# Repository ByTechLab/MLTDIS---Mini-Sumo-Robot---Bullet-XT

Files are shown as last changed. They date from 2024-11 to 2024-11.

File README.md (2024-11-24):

<div align="center">
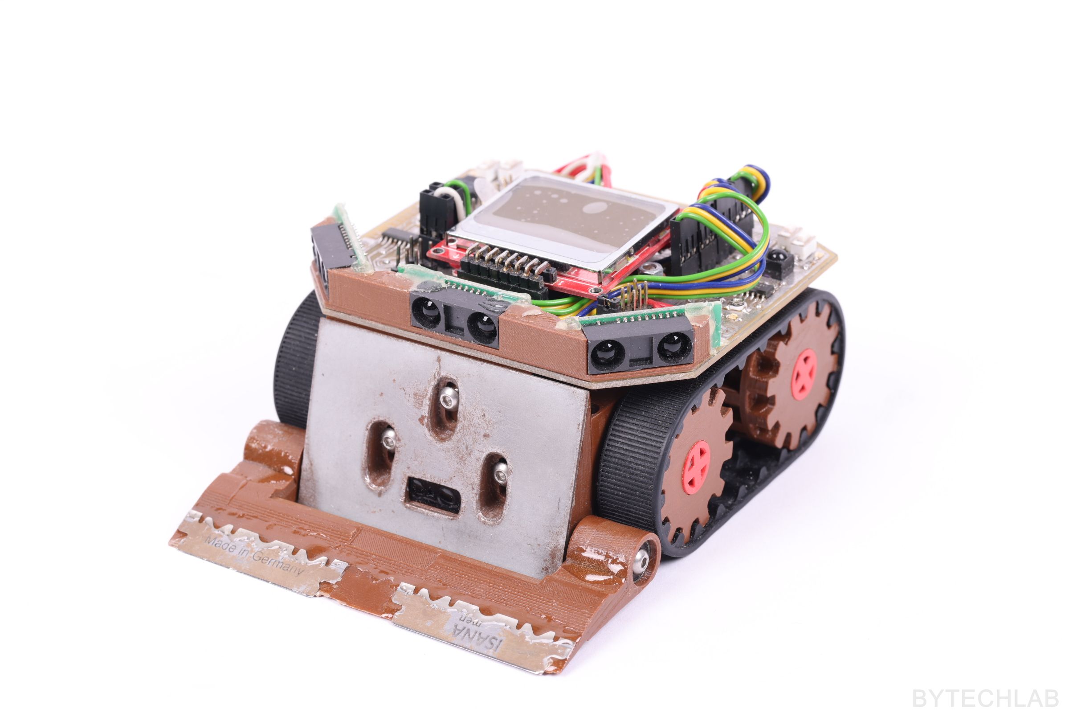
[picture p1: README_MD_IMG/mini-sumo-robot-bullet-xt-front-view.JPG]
project photo
    
</div>

Mini sumo robot - Bullet XT.

### Read more at BYTECHLAB:

<table style="width: 100%; border: none;" cellspacing="0" cellpadding="0" border="0">
  <tr>
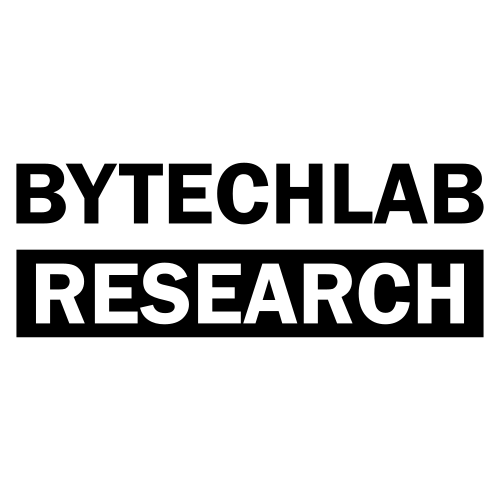
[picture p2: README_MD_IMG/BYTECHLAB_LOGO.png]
    <td></td>
    <td>https://bytechlab.com/2017/09/minisumo-bullet-xt/</td>
  </tr>
</table>

## License
Software \ Firmware:



Hardware \ Hardware design files \ Hardware documentation:

[][cc-by-nc-sa]

[Creative Commons Attribution-NonCommercial-ShareAlike 4.0 International License][cc-by-nc-sa].

[][cc-by-nc-sa]

[cc-by-nc-sa]: http://creativecommons.org/licenses/by-nc-sa/4.0/
[cc-by-nc-sa-image]: https://licensebuttons.net/l/by-nc-sa/4.0/88x31.png
[cc-by-nc-sa-shield]: https://img.shields.io/badge/License-CC%20BY--NC--SA%204.0-lightgrey.svg

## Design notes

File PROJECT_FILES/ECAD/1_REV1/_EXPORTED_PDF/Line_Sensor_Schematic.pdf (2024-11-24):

## 24.11.2024 15:51 (Sheet: 1/1)

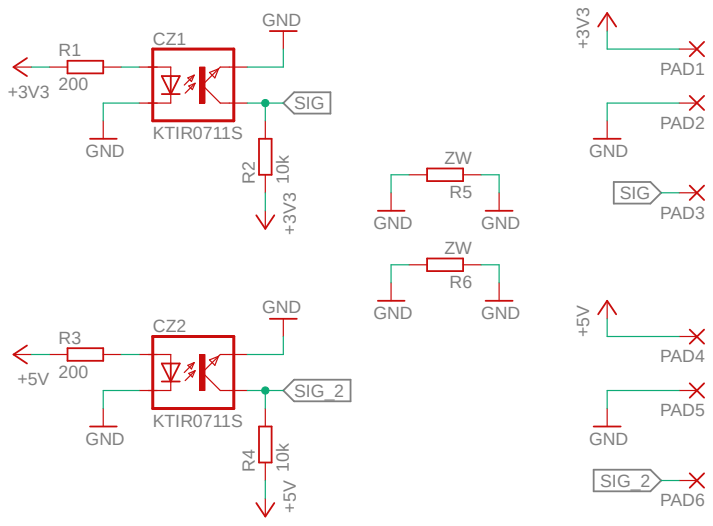
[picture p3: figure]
KTIR0711S; GND; PAD1; PAD2; PAD3; PAD4; PAD5; PAD6; SIG; SIG_2

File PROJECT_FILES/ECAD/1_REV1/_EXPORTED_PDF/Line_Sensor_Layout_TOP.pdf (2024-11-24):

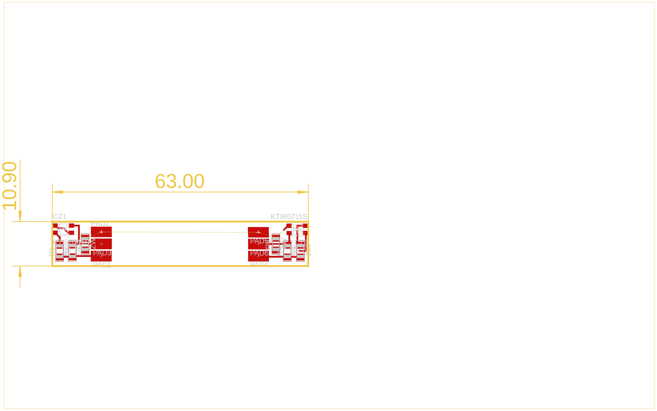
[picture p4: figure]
PAD1; PAD2 R¹; PAD4; KTIR0711S; KTIR0711S 200 10.90

24.11.2024 15:52

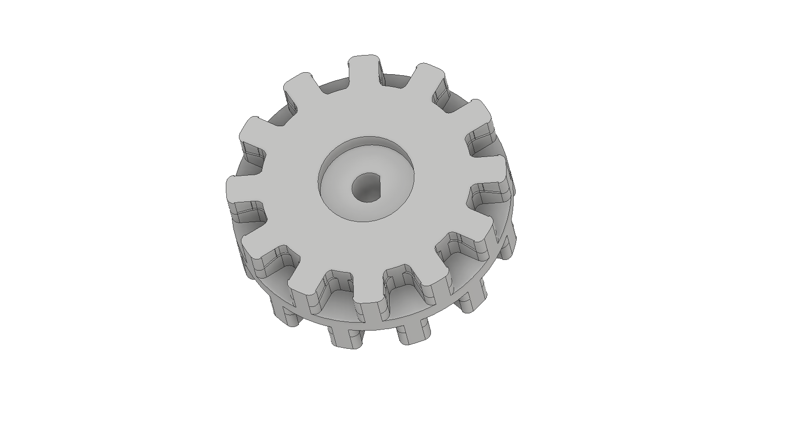
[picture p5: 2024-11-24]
PROJECT_FILES/MCAD/1_REV1/_RENDERS_EXPORTED/3DP_PLA_Motor_wheel.bmp

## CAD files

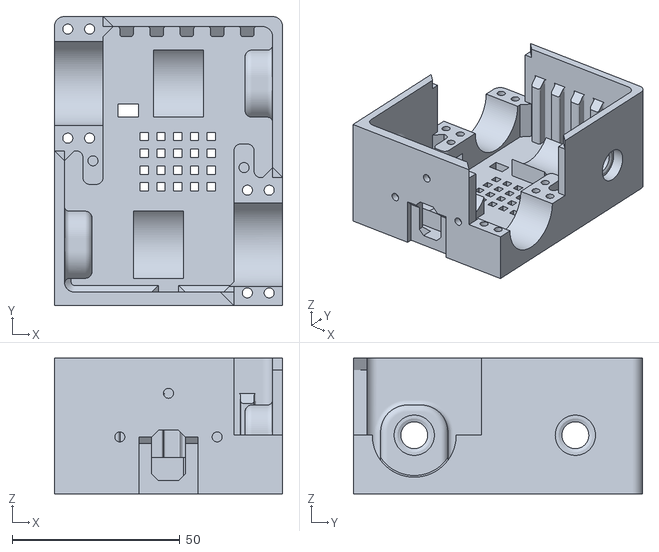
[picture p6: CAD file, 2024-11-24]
PROJECT_FILES/MCAD/1_REV1/_STL_EXPORTED/3DP_PLA_Main_frame.stl
68.0 x 86.1 x 40.5

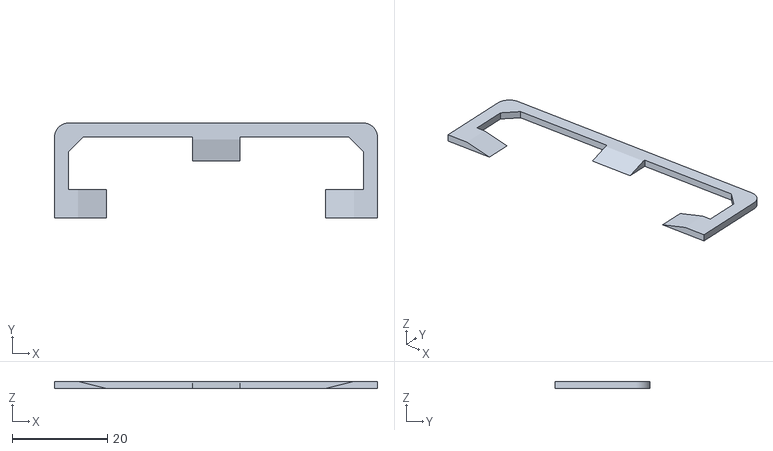
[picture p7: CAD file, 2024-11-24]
PROJECT_FILES/MCAD/1_REV1/_STL_EXPORTED/3DP_PLA_Back_slider.stl
68.0 x 20.0 x 1.50

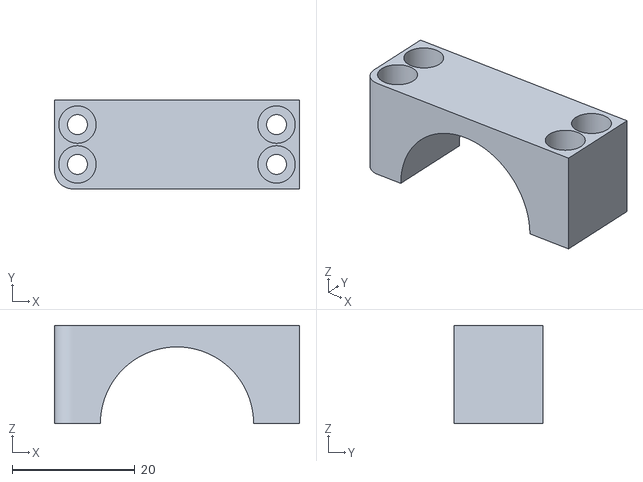
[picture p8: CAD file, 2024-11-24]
PROJECT_FILES/MCAD/1_REV1/_STL_EXPORTED/3DP_PLA_Motor_mounting_bracket_back.stl
40.0 x 14.5 x 16.0

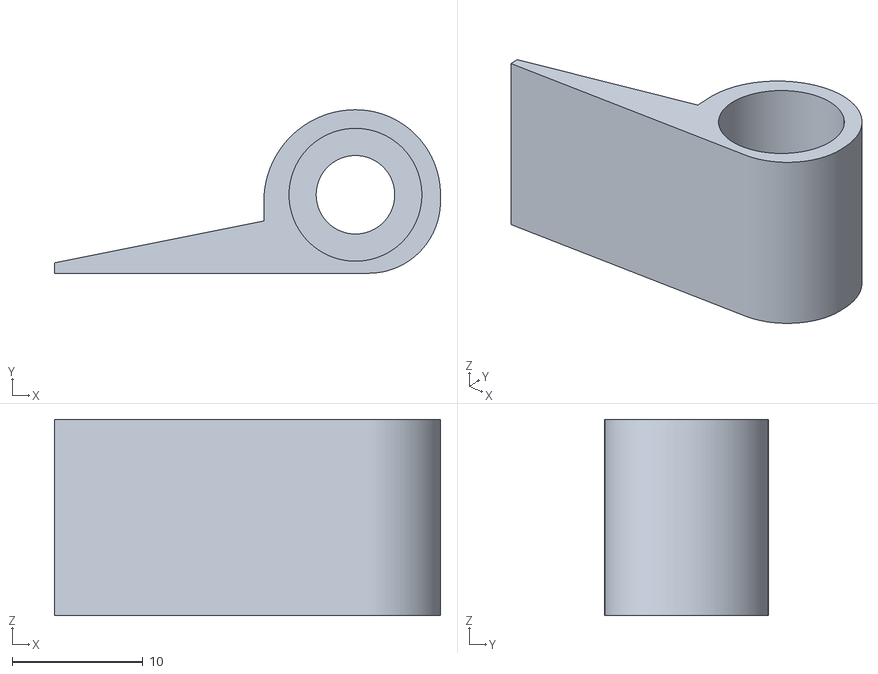
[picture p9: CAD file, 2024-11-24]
PROJECT_FILES/MCAD/1_REV1/_STL_EXPORTED/3DP_PLA_Front_blade_hinge_mir.stl
29.5 x 12.5 x 15.0

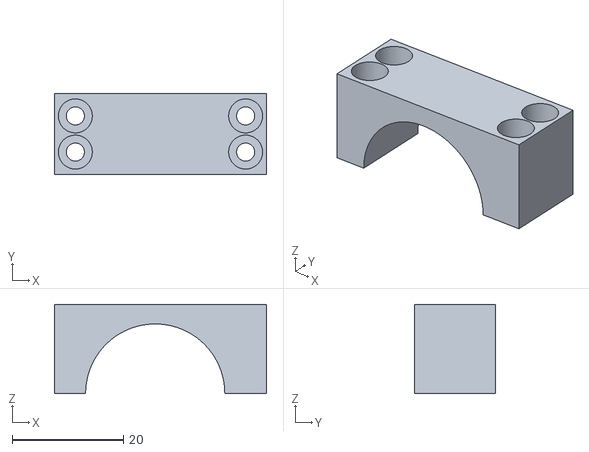
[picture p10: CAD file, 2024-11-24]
PROJECT_FILES/MCAD/1_REV1/_STL_EXPORTED/3DP_PLA_Motor_mounting_bracket_front.stl
38.1 x 14.5 x 16.0

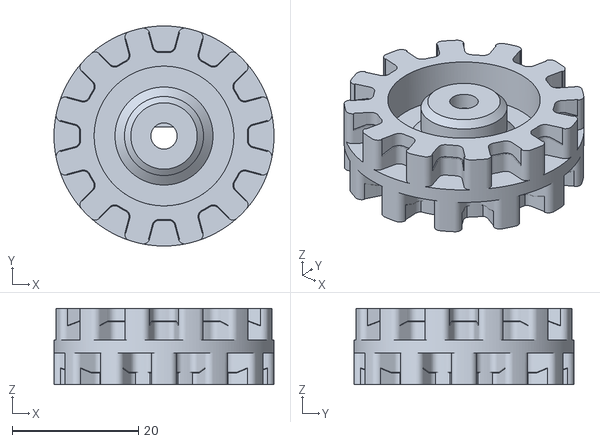
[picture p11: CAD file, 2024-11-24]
PROJECT_FILES/MCAD/1_REV1/_STL_EXPORTED/3DP_PLA_Motor_wheel.stl
34.8 x 34.8 x 12.0

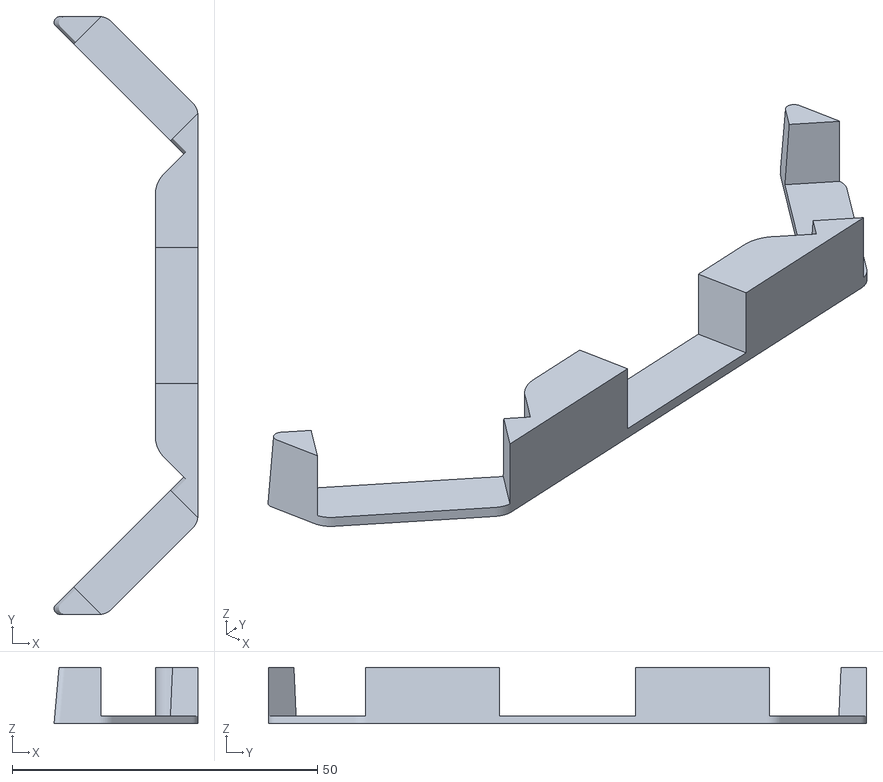
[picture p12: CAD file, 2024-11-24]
PROJECT_FILES/MCAD/1_REV1/_STL_EXPORTED/3DP_PLA_Front_Sharp_sensors_mounting_bracket.stl
23.6 x 98.0 x 9.20

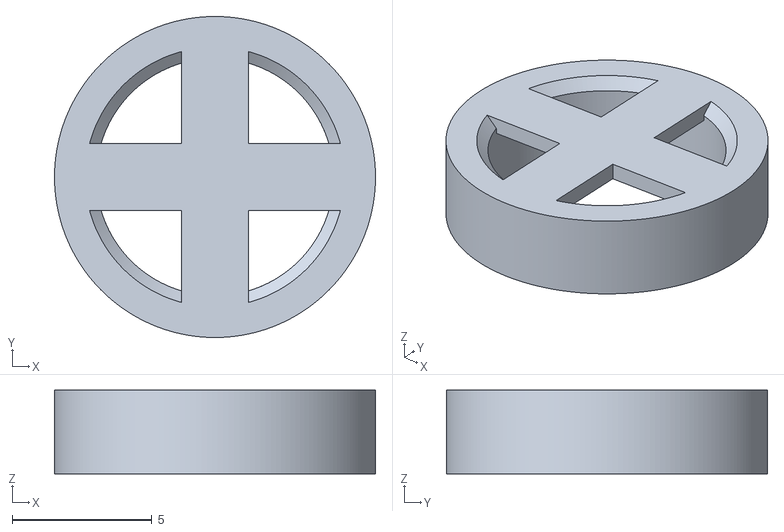
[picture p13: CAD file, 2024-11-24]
PROJECT_FILES/MCAD/1_REV1/_STL_EXPORTED/3DP_PLA_Wheel_cover.stl
11.5 x 11.5 x 3.00

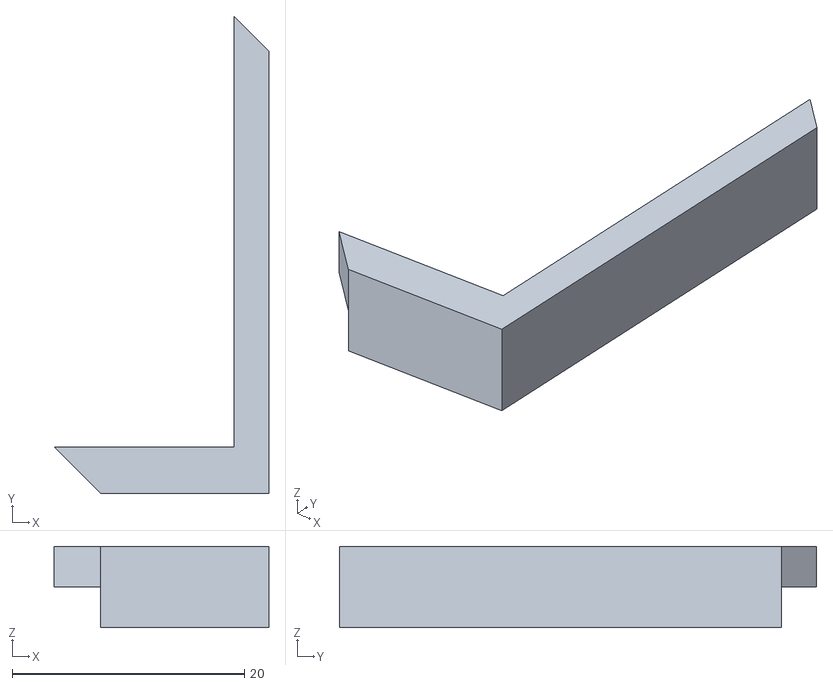
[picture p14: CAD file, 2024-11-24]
PROJECT_FILES/MCAD/1_REV1/_STL_EXPORTED/3DP_PLA_Front_motor_clamp_hole_plug.stl
18.5 x 41.1 x 7.00

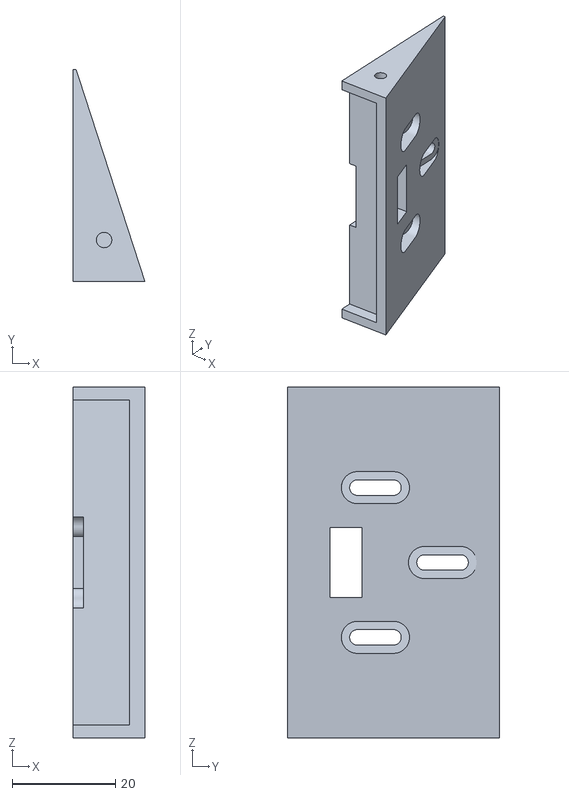
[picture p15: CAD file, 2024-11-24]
PROJECT_FILES/MCAD/1_REV1/_STL_EXPORTED/3DP_PLA_Front_plow.stl
13.9 x 41.0 x 68.0

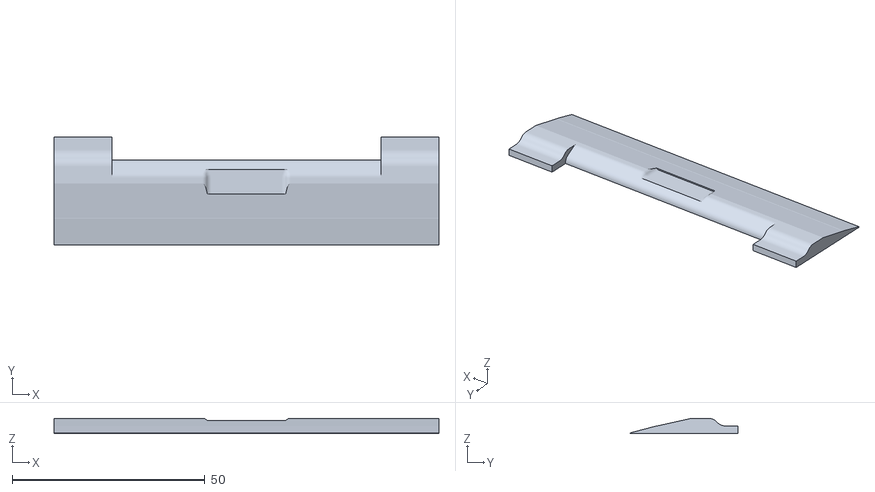
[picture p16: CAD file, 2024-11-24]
PROJECT_FILES/MCAD/1_REV1/_STL_EXPORTED/3DP_PLA_Front_blade.stl
100.0 x 28.0 x 4.00

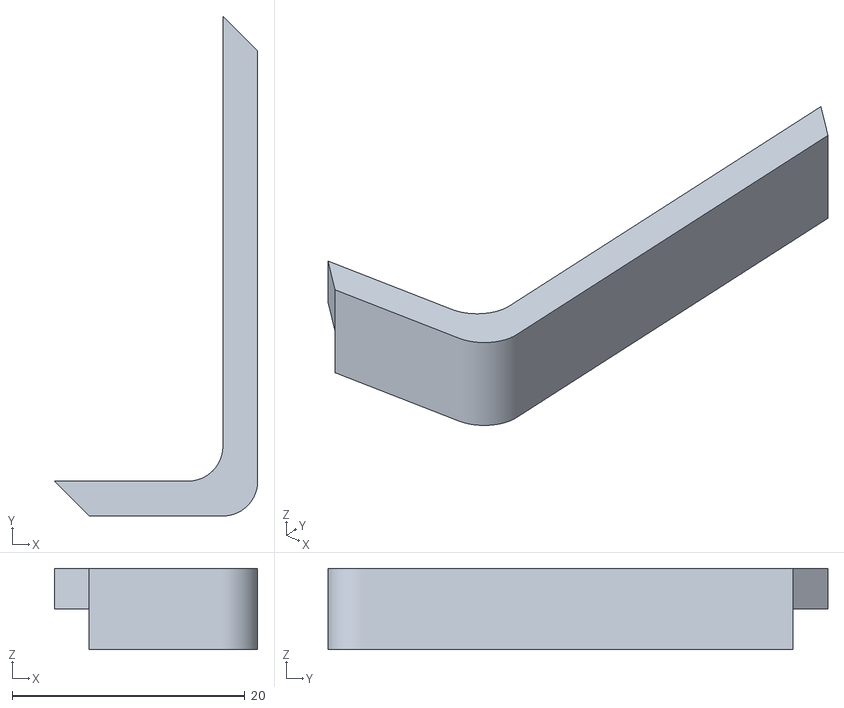
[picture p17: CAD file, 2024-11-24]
PROJECT_FILES/MCAD/1_REV1/_STL_EXPORTED/3DP_PLA_Back_motor_clamp_hole_plug.stl
17.5 x 43.0 x 7.00

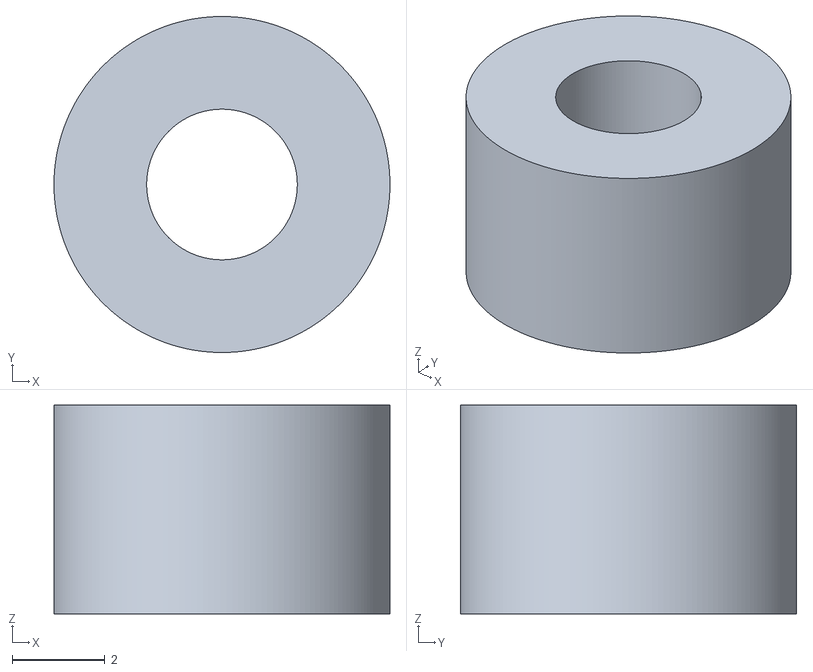
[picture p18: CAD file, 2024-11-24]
PROJECT_FILES/MCAD/1_REV1/_STL_EXPORTED/3DP_PLA_M3_screw_washer.stl
7.25 x 7.25 x 4.50

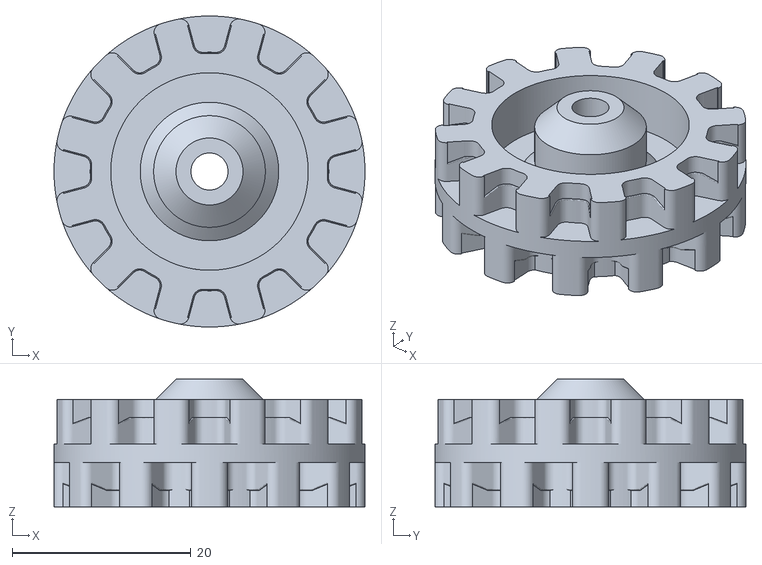
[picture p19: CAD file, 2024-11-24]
PROJECT_FILES/MCAD/1_REV1/_STL_EXPORTED/3DP_PLA_Screw_wheel.stl
34.8 x 34.8 x 14.3

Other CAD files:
PROJECT_FILES/MCAD/1_REV1/_STL_EXPORTED/3DP_PLA_Front_blade_hinge.stl
PROJECT_FILES/MCAD/1_REV1/ASSEMBLY_MAIN_REVA/3DP_PLA_Back_motor_clamp_hole_plug.ipt
PROJECT_FILES/MCAD/1_REV1/ASSEMBLY_MAIN_REVA/3DP_PLA_Back_slider.ipt
PROJECT_FILES/MCAD/1_REV1/ASSEMBLY_MAIN_REVA/3DP_PLA_Front_Sharp_sensors_mounting_bracket.ipt
PROJECT_FILES/MCAD/1_REV1/ASSEMBLY_MAIN_REVA/3DP_PLA_Front_blade.ipt
PROJECT_FILES/MCAD/1_REV1/ASSEMBLY_MAIN_REVA/3DP_PLA_Front_blade_hinge.ipt
PROJECT_FILES/MCAD/1_REV1/ASSEMBLY_MAIN_REVA/3DP_PLA_Front_blade_hinge_mir.ipt
PROJECT_FILES/MCAD/1_REV1/ASSEMBLY_MAIN_REVA/3DP_PLA_Front_motor_clamp_hole_plug.ipt
PROJECT_FILES/MCAD/1_REV1/ASSEMBLY_MAIN_REVA/3DP_PLA_Front_plow.ipt
PROJECT_FILES/MCAD/1_REV1/ASSEMBLY_MAIN_REVA/3DP_PLA_M3_screw_washer.ipt
PROJECT_FILES/MCAD/1_REV1/ASSEMBLY_MAIN_REVA/3DP_PLA_Main_frame.ipt
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

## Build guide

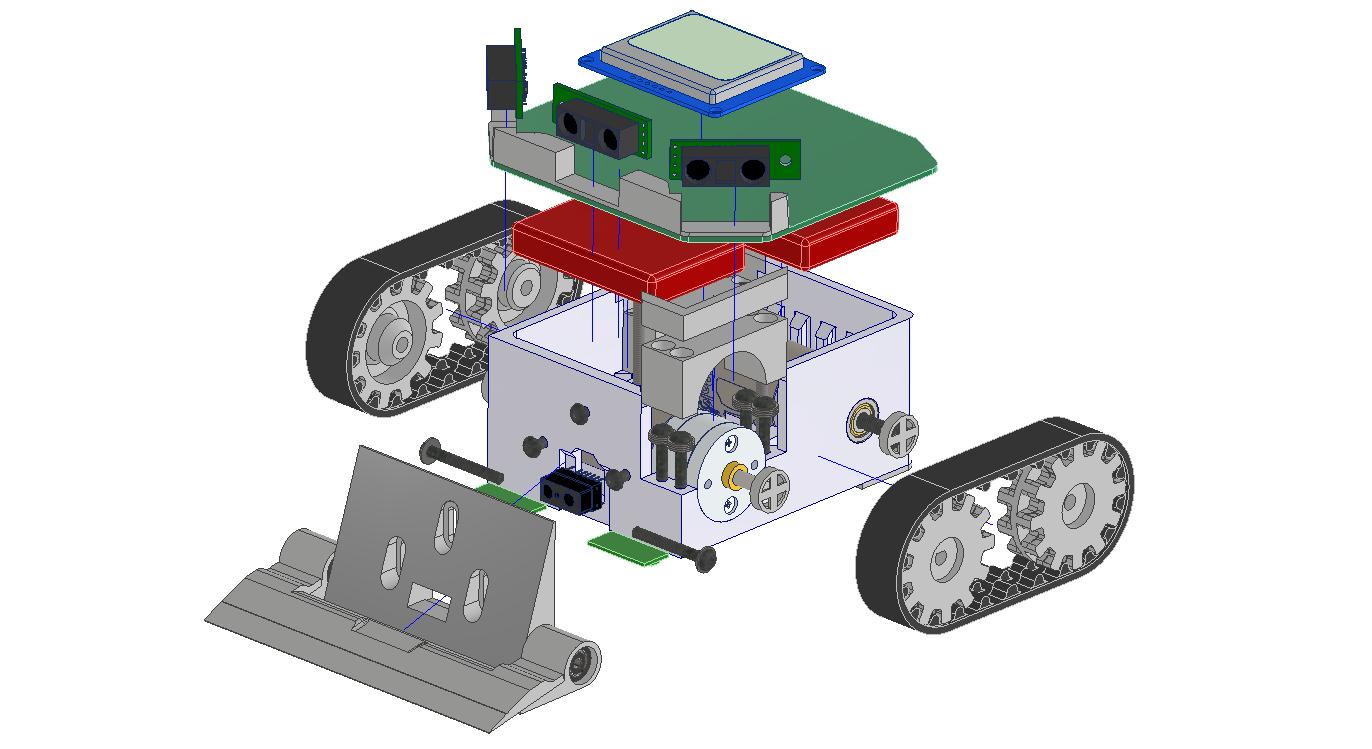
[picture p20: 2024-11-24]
PROJECT_FILES/MCAD/1_REV1/_RENDERS_EXPORTED/ASSEMBLY_Main_4.bmp

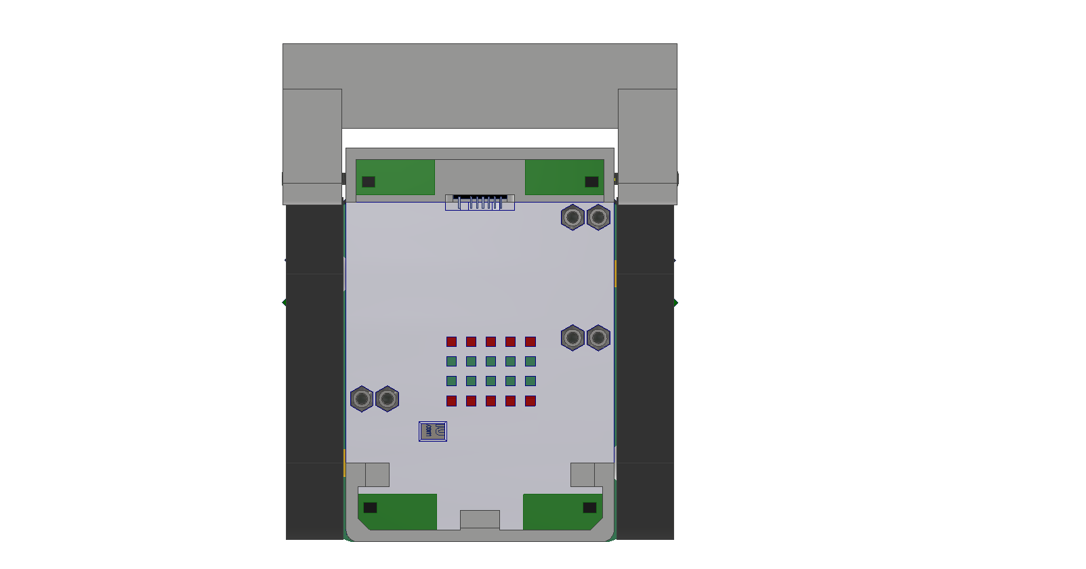
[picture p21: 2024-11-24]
PROJECT_FILES/MCAD/1_REV1/_RENDERS_EXPORTED/ASSEMBLY_Main_3.bmp

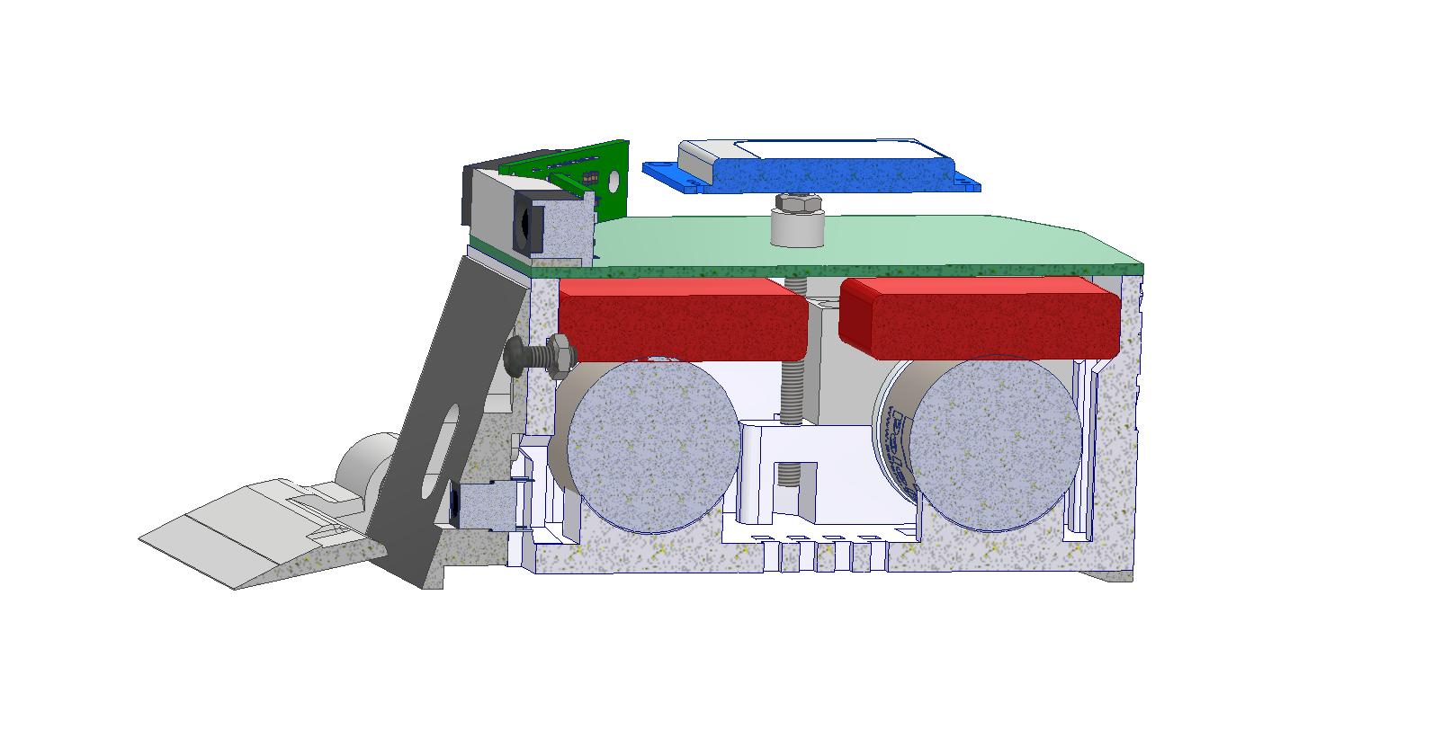
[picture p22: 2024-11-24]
PROJECT_FILES/MCAD/1_REV1/_RENDERS_EXPORTED/ASSEMBLY_Main_2.bmp

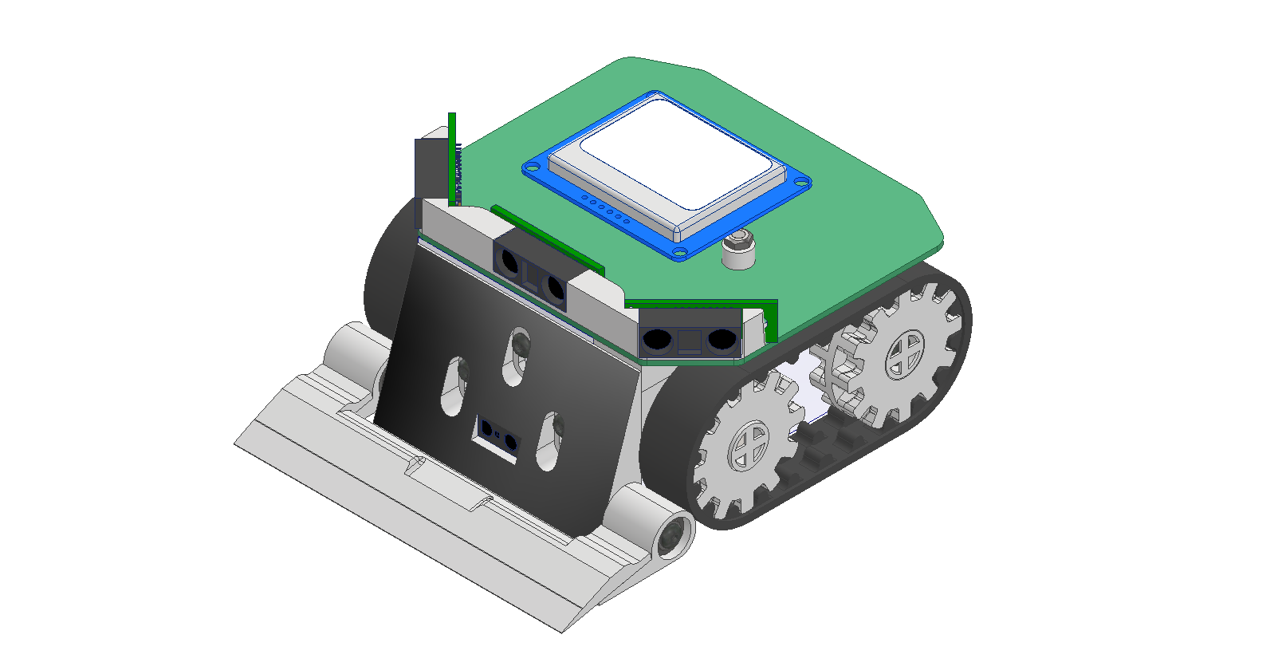
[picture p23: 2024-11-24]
PROJECT_FILES/MCAD/1_REV1/_RENDERS_EXPORTED/ASSEMBLY_Main.bmp

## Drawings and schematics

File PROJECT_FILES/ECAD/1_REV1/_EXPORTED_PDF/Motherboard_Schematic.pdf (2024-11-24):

# GND BATV BATV

## BUZZER

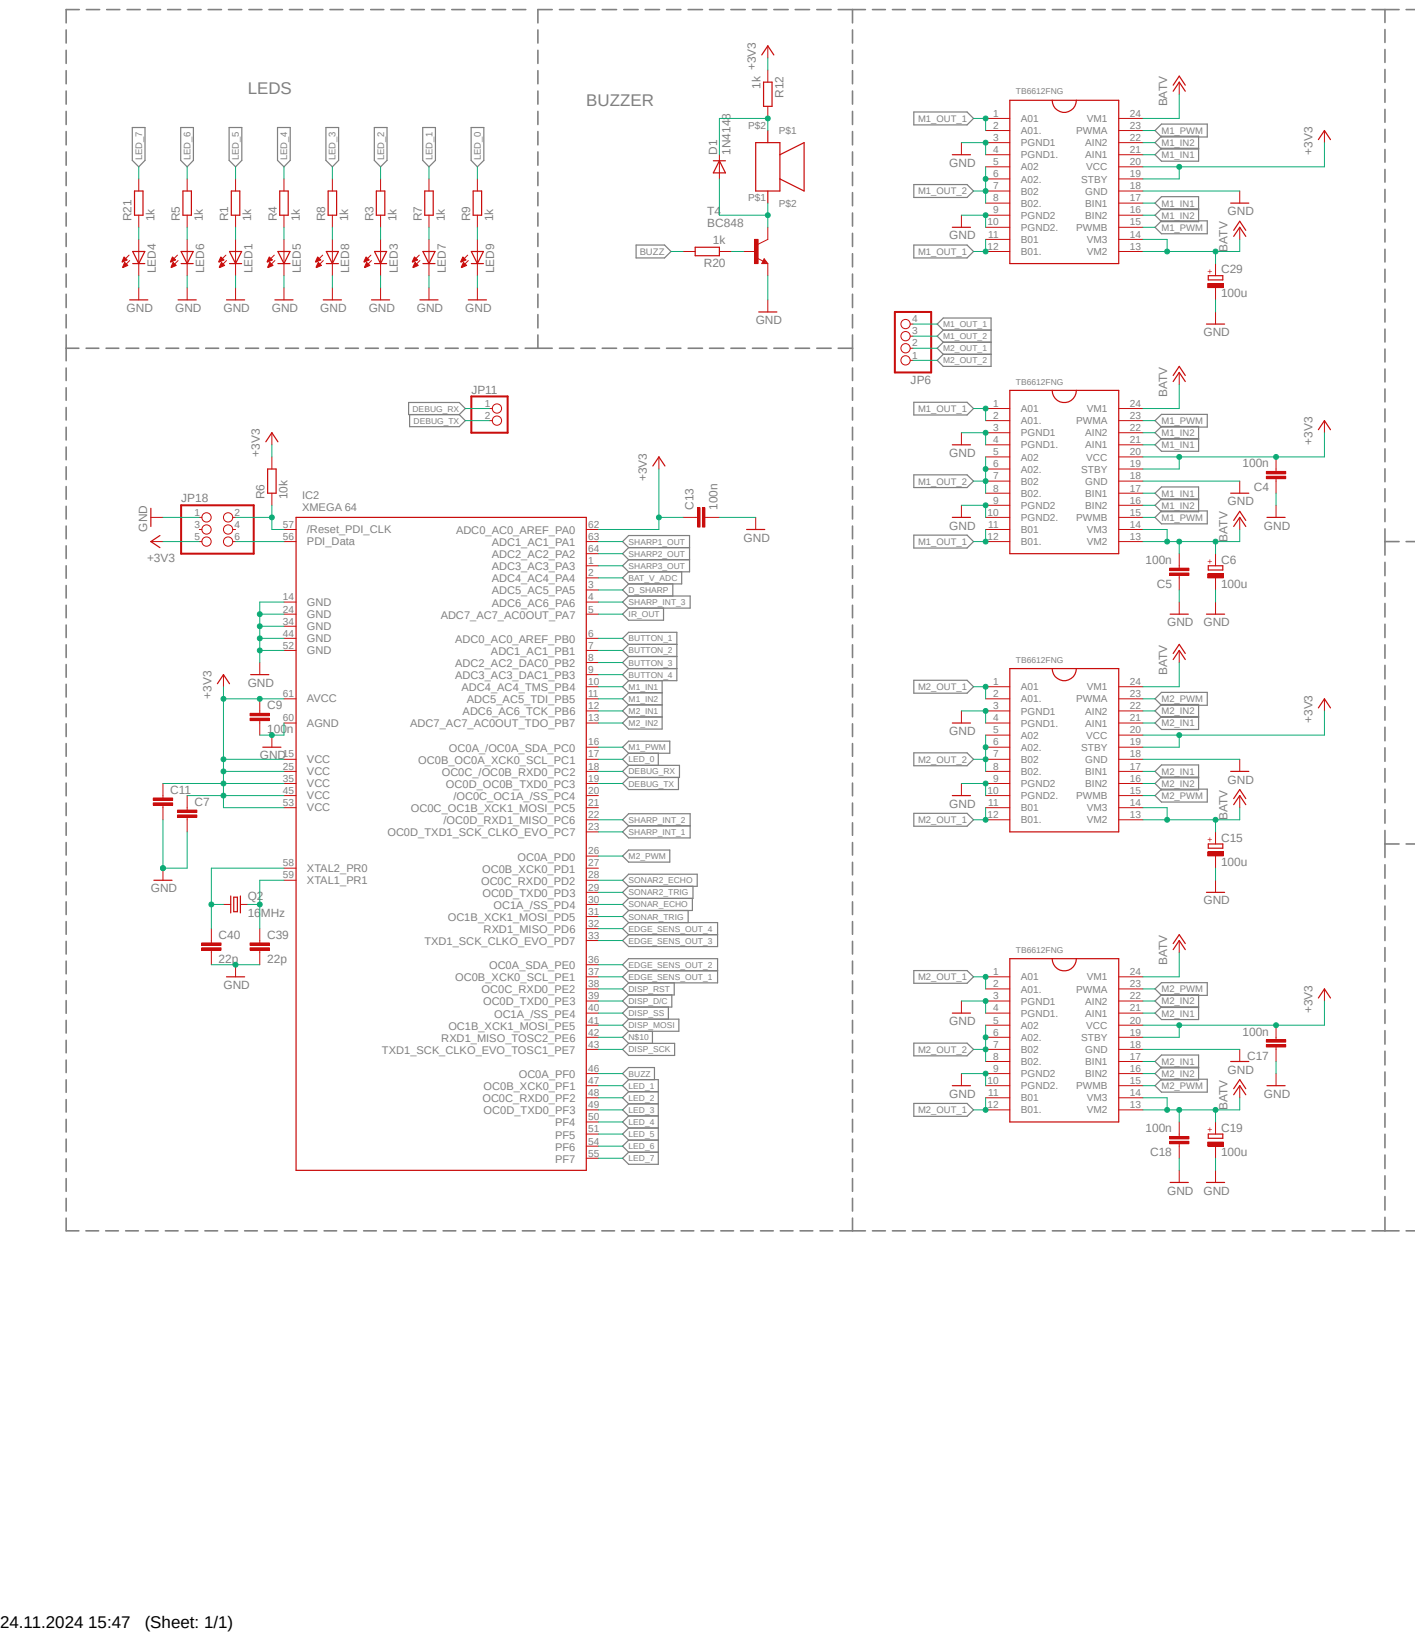
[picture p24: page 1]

45
53

## EDGE SENS

IR

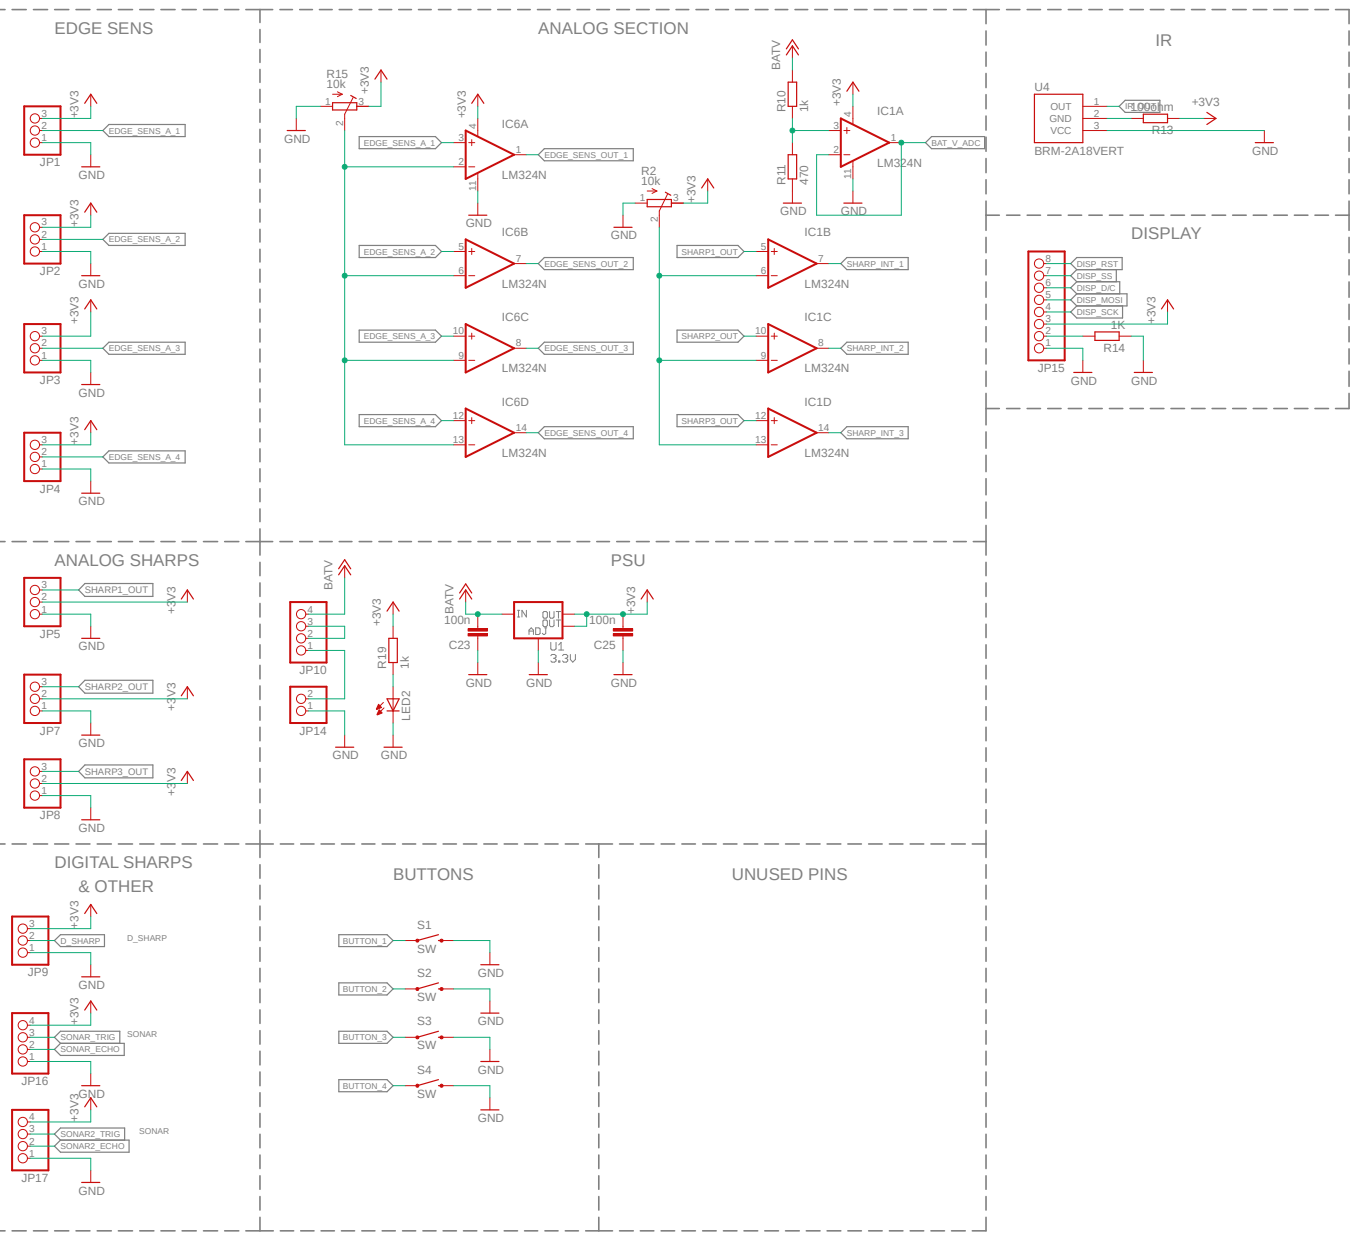
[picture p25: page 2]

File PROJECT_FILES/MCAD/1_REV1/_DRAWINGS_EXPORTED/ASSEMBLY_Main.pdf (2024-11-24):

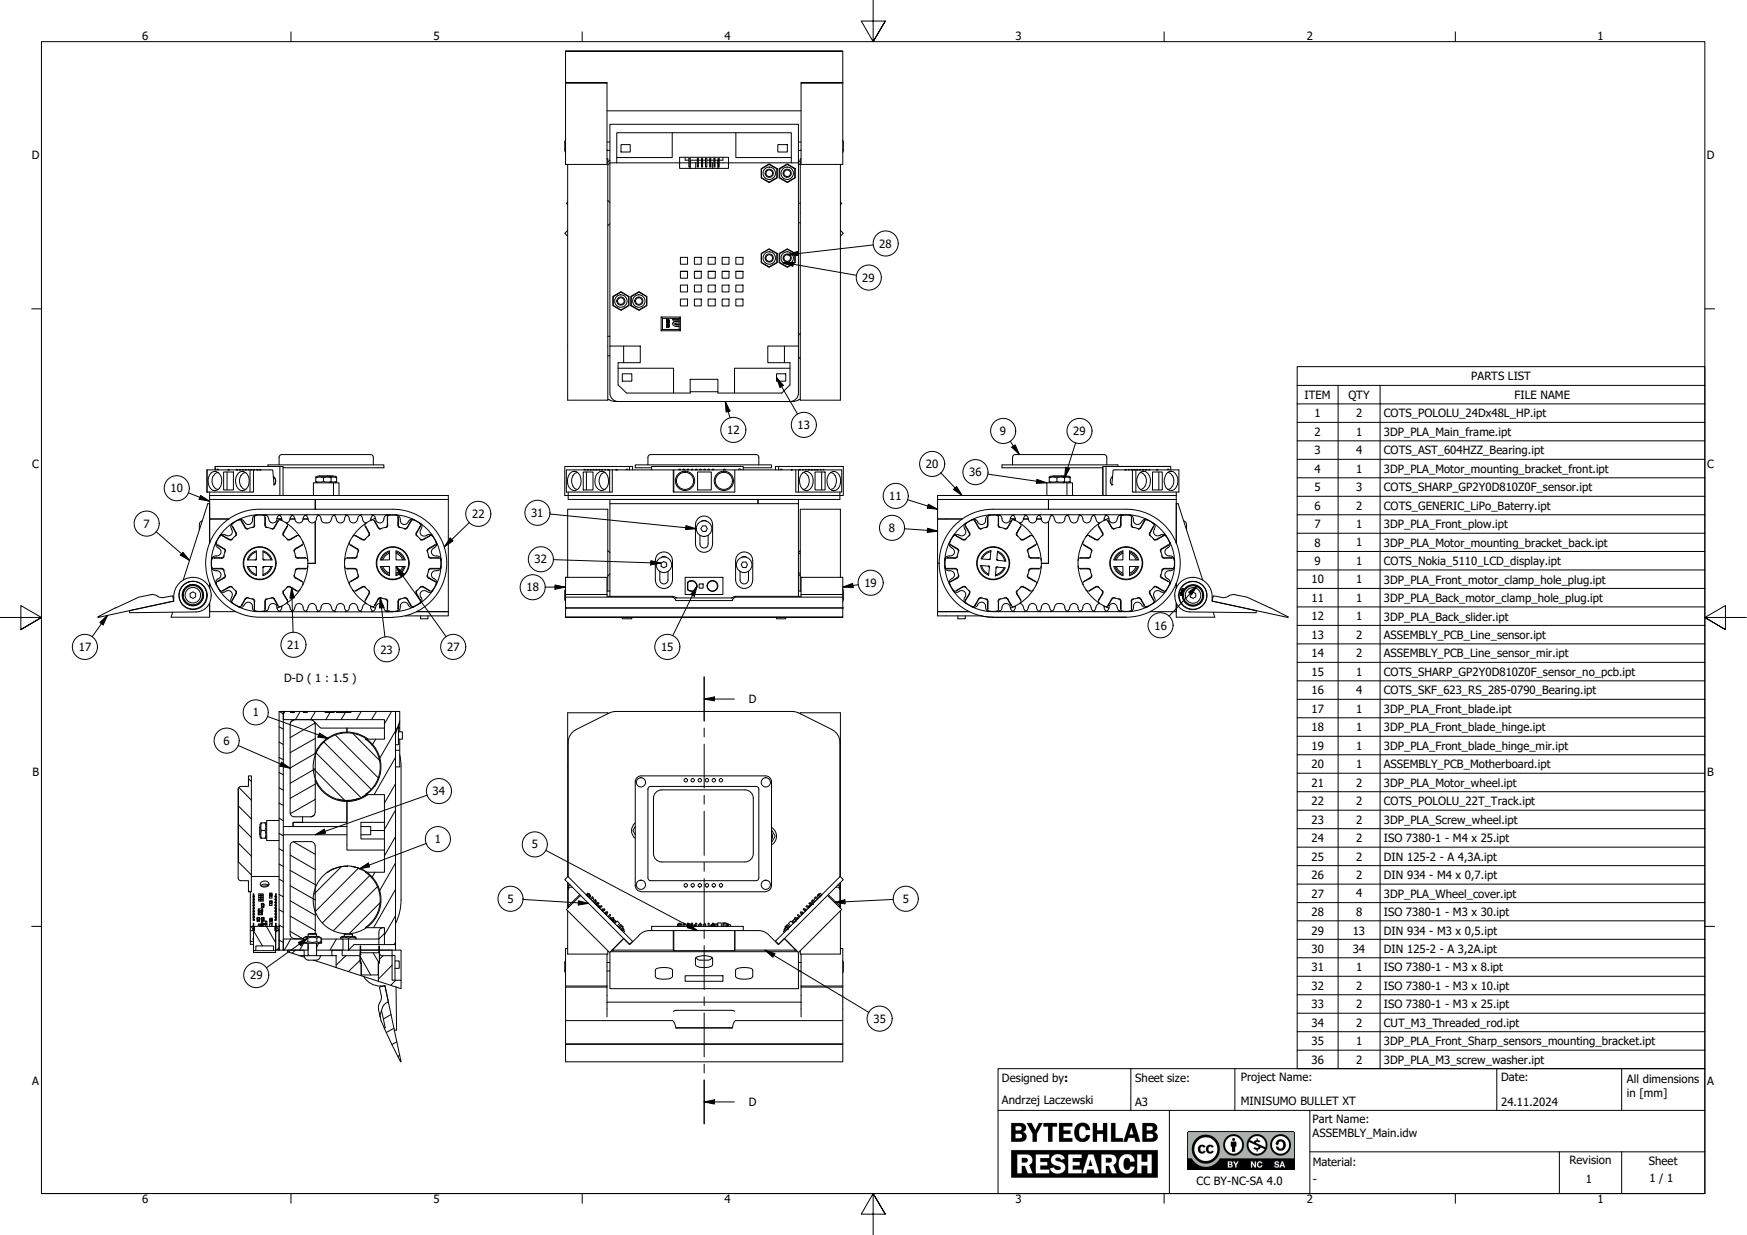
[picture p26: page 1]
PARTS LIST; ITEM; QTY; FILE NAME

2 | 1 | 3DP_PLA_Main_frame.ipt
3 | 4 | COTS_AST_604HZZ_Bearing.ipt
4 | 1 | 3DP_PLA_Motor_mounting_bracket_front.ipt
5 | 3 | COTS_SHARP_GP2Y0D810Z0F_sensor.ipt
6 | 2 | COTS_GENERIC_LiPo_Baterry.ipt
7 | 1 | 3DP_PLA_Front_plow.ipt
8 | 1 | 3DP_PLA_Motor_mounting_bracket_back.ipt
9 | 1 | COTS_Nokia_5110_LCD_display.ipt
10 | 1 | 3DP_PLA_Front_motor_clamp_hole_plug.ipt
11 | 1 | 3DP_PLA_Back_motor_clamp_hole_plug.ipt
12 | 1 | 3DP_PLA_Back_slider.ipt
13 | 2 | ASSEMBLY_PCB_Line_sensor.ipt
14 | 2 | ASSEMBLY_PCB_Line_sensor_mir.ipt
15 | 1 | COTS_SHARP_GP2Y0D810Z0F_sensor_no_pcb.ipt
16 | 4 | COTS_SKF_623_RS_285-0790_Bearing.ipt
17 | 1 | 3DP_PLA_Front_blade.ipt
18 | 1 | 3DP_PLA_Front_blade_hinge.ipt
19 | 1 | 3DP_PLA_Front_blade_hinge_mir.ipt
20 | 1 | ASSEMBLY_PCB_Motherboard.ipt
21 | 2 | 3DP_PLA_Motor_wheel.ipt
22 | 2 | COTS_POLOLU_22T_Track.ipt
23 | 2 | 3DP_PLA_Screw_wheel.ipt
24 | 2 | ISO 7380-1 - M4 x 25.ipt
25 | 2 | DIN 125-2 - A 4,3A.ipt
26 | 2 | DIN 934 - M4 x 0,7.ipt
27 | 4 | 3DP_PLA_Wheel_cover.ipt
28 | 8 | ISO 7380-1 - M3 x 30.ipt
29 | 13 | DIN 934 - M3 x 0,5.ipt
30 | 34 | DIN 125-2 - A 3,2A.ipt
31 | 1 | ISO 7380-1 - M3 x 8.ipt
32 | 2 | ISO 7380-1 - M3 x 10.ipt
33 | 2 | ISO 7380-1 - M3 x 25.ipt
34 | 2 | CUT_M3_Threaded_rod.ipt
35 | 1 | 3DP_PLA_Front_Sharp_sensors_mounting_bracket.ipt
36 | 2 | 3DP_PLA_M3_screw_washer.ipt

Designed by: Andrzej Laczewski | Sheet size: A3 | Project Name: MINISUMO BULLET XT | Date: 24.11.2024 | All dimensions in [mm]

CC BY-NC-SA 4.0 | Part Name: ASSEMBLY_Main.idw

Material: - 1 | Revision | Sheet 1 / 1

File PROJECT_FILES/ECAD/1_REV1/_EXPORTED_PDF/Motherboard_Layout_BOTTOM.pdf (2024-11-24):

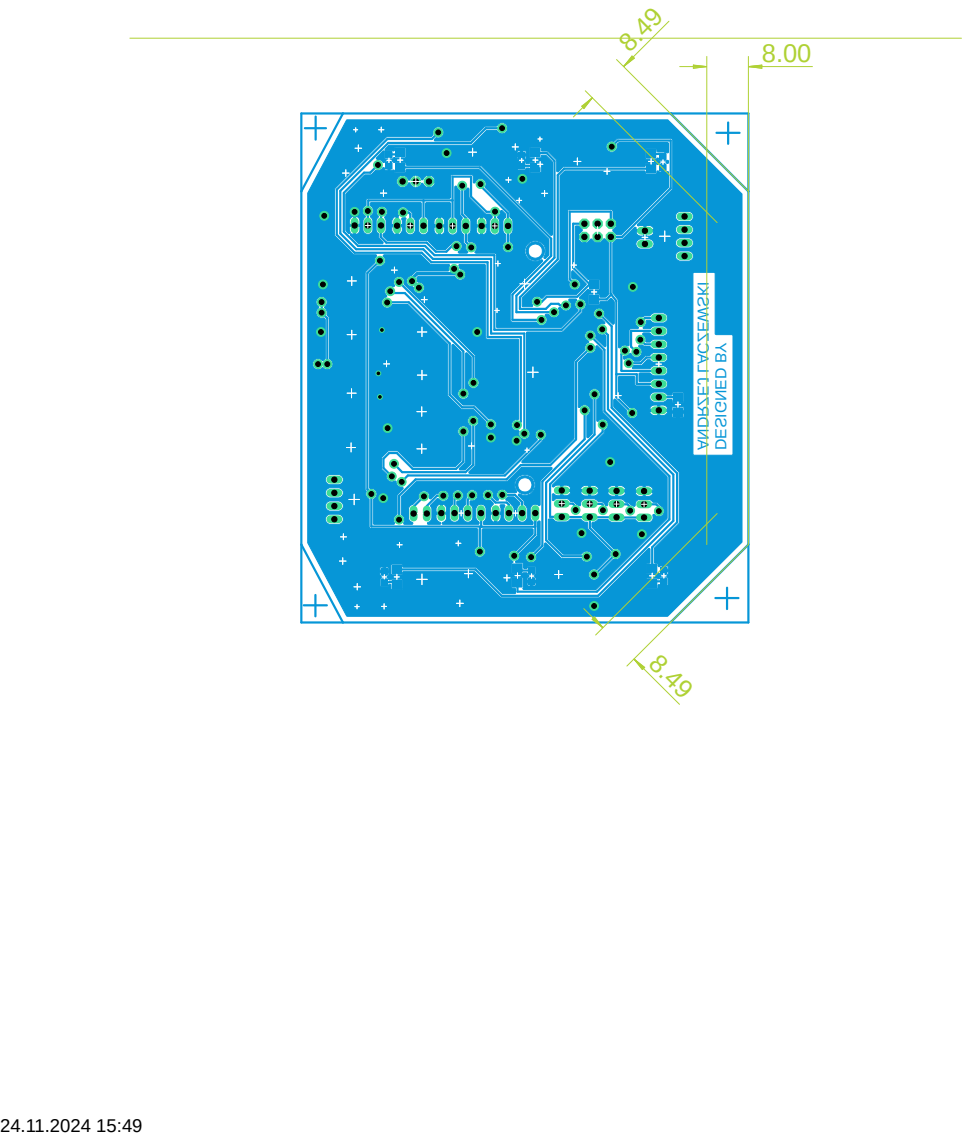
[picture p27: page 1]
ANDRZEJ LACZEWSKI DESIGNED BY

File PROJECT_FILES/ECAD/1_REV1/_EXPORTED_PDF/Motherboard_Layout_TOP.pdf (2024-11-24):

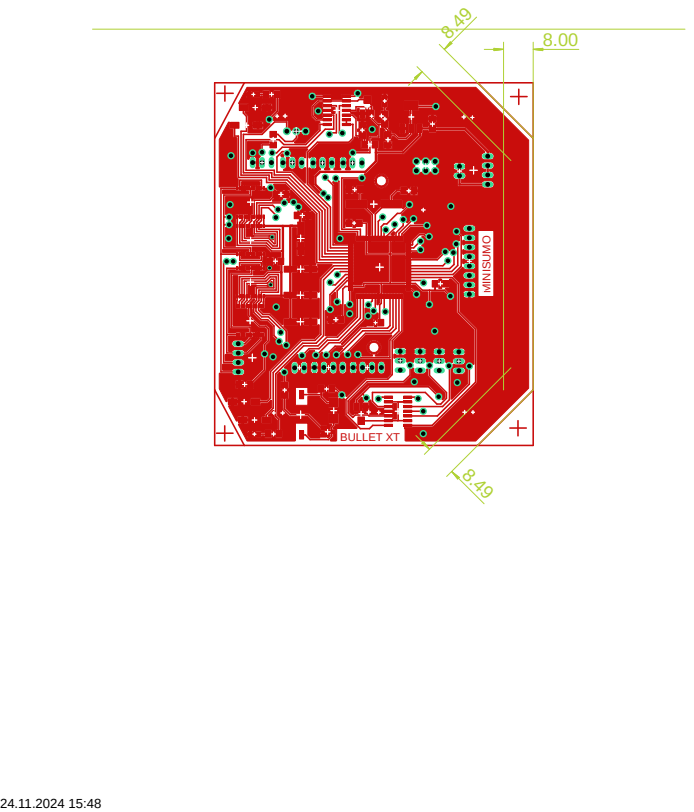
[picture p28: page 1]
BULLET XT; MINISUMO

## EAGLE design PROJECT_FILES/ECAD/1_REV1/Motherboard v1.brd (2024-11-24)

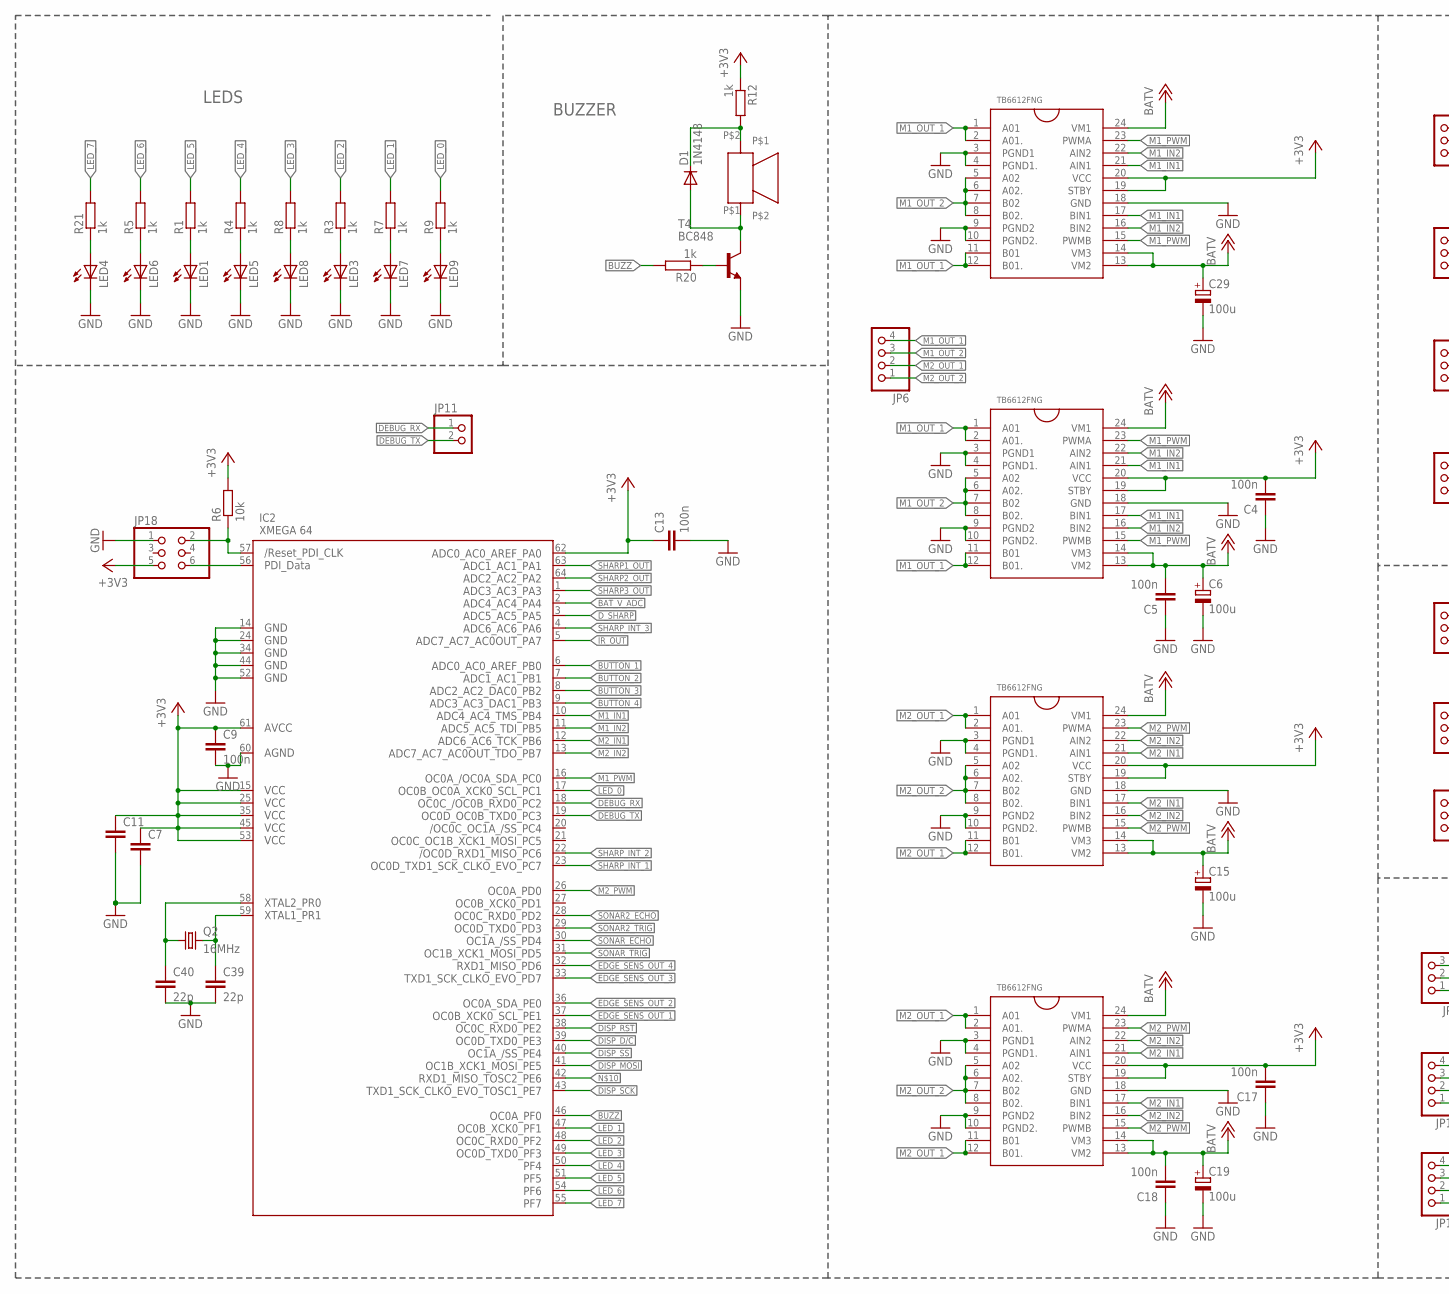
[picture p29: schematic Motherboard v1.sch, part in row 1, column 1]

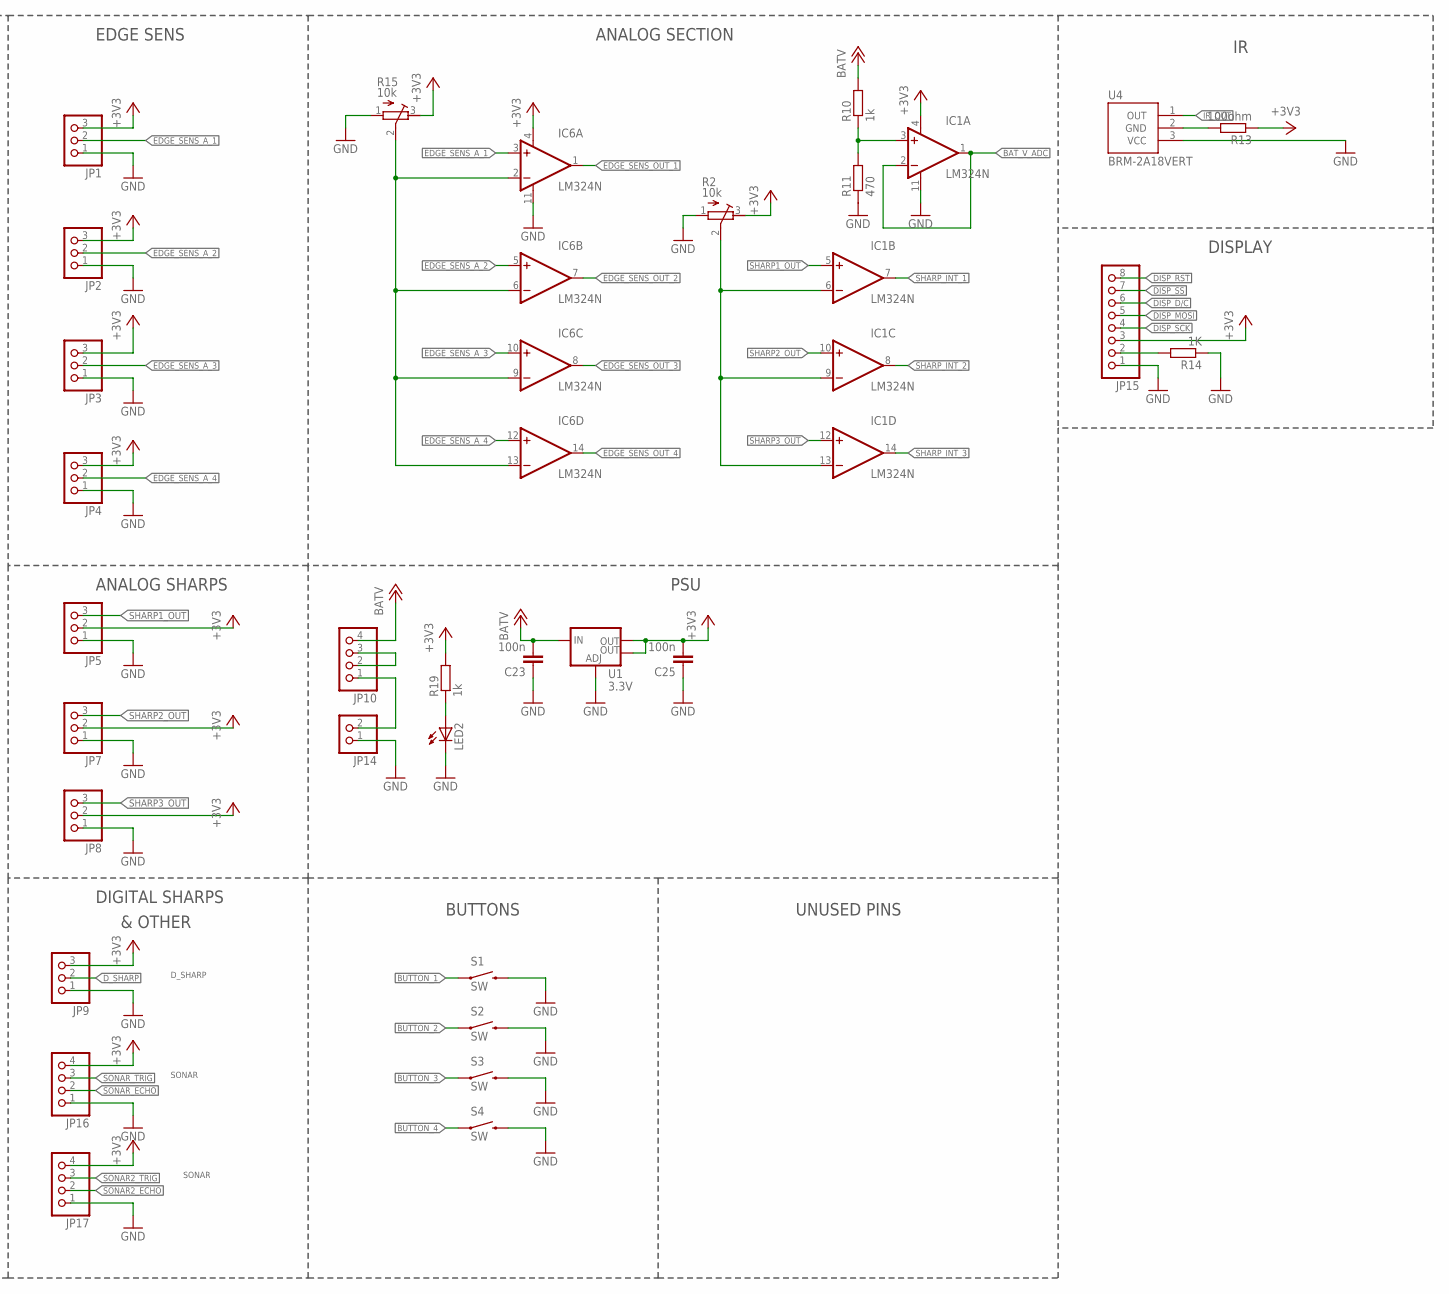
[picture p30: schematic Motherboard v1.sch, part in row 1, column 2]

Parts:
C4, C5, C9, C13, C17, C18, C23, C25: 100n; C1206
C6, C15, C19, C29: 100u; 153CLV-0605
C7, C11: C-EUC1206; C1206
C39, C40: 22p; C1206
D1: 1N4148; SMB
IC1: LM324N; SO14; MPN OPA4130UA
IC2: XMEGA 64; TQFP64
IC6: LM324N; SO14
JP1, JP2, JP3, JP4, JP5, JP7, JP8, JP9: PINHD-1X3; 1X03
JP6, JP10: PINHD-1X4/90; 1X04/90
JP11, JP14: PINHD-1X2; 1X02
JP15: PINHD-1X8; 1X08
JP16, JP17: PINHD-1X4; 1X04
JP18: PINHD-2X3; 2X03
LED1, LED2, LED3, LED4, LED5, LED7, LED9: LEDCHIPLED_0805; CHIPLED_0805
LED6, LED8: LEDCHIP-LED0805; CHIP-LED0805
Q2: 16MHz; CSM-7X-DU
R1, R3, R4, R5, R7, R8, R9, R10, R12, R19, R20, R21: 1k; R1206
R2, R15: 10k; RTRIMTSM53YL
R6: 10k; R1206
R11: 470; R1206
R13: 100ohm; R1206
R14: 1K; R1206
S1, S2, S3, S4: SW; TACTILE-SWITCH-1101NE
T4: BC848; SOT23
U1: 3.3V; SOT223
U4: BRM-2A18VERT; BRM-2508_VERT
U$1, U$2, U$3, U$4: TB6612FNG; SSOP24
U$13: BOT-03; BOT-03D

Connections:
+3V3: C4.2, C7.1, C9.1, C11.1, C13.1, C17.2, C25.2, IC1.4 (V+), IC2.15 (VCC1), IC2.25 (VCC2), IC2.35 (VCC3), IC2.45 (VCC4), IC2.53 (VCC5), IC2.61 (AVCC), IC2.62 (PA0), IC6.4 (V+), JP1.3, JP2.3, JP3.3, JP4.3, JP5.2, JP7.2, JP8.2, JP9.3, JP15.3, JP16.4, JP17.4, JP18.5, R2.3 (E), R6.2, R12.1, R13.1, R15.3 (E), R19.2, U1.2 (OUT), U1.4 (OUT), U$1.19 (STBY), U$1.20 (VCC), U$2.19 (STBY), U$2.20 (VCC), U$3.19 (STBY), U$3.20 (VCC), U$4.19 (STBY), U$4.20 (VCC)
+12V: C5.2, C6.+, C15.+, C18.2, C19.+, C23.2, C29.+, JP10.4, R10.2, U1.3 (IN), U$1.13 (VM2), U$1.14 (VM3), U$1.24 (VM1), U$2.13 (VM2), U$2.14 (VM3), U$2.24 (VM1), U$3.13 (VM2), U$3.14 (VM3), U$3.24 (VM1), U$4.13 (VM2), U$4.14 (VM3), U$4.24 (VM1)
BAT_V_ADC: IC1.1 (OUT), IC1.2 (-IN), IC2.2 (PA4)
BUTTON_1: IC2.6 (PB0), S1.1
BUTTON_2: IC2.7 (PB1), S2.1
BUTTON_3: IC2.8 (PB2), S3.1
BUTTON_4: IC2.9 (PB3), S4.1
BUZZ: IC2.46 (PF0), R20.2
DEBUG_RX: IC2.18 (PC2), JP11.1
DEBUG_TX: IC2.19 (PC3), JP11.2
DISP_D/C: IC2.39 (PE3), JP15.6
DISP_MOSI: IC2.41 (PE5), JP15.5
DISP_RST: IC2.38 (PE2), JP15.8
DISP_SCK: IC2.43 (PE7), JP15.4
DISP_SS: IC2.40 (PE4), JP15.7
D_SHARP: IC2.3 (PA5), JP9.2
EDGE_SENS_A_1: IC6.3 (+IN), JP1.2
EDGE_SENS_A_2: IC6.5 (+IN), JP2.2
EDGE_SENS_A_3: IC6.10 (+IN), JP3.2
EDGE_SENS_A_4: IC6.12 (+IN), JP4.2
EDGE_SENS_OUT_1: IC2.37 (PE1), IC6.1 (OUT)
EDGE_SENS_OUT_2: IC2.36 (PE0), IC6.7 (OUT)
EDGE_SENS_OUT_3: IC2.33 (PD7), IC6.8 (OUT)
EDGE_SENS_OUT_4: IC2.32 (PD6), IC6.14 (OUT)
GND: C4.1, C5.1, C6.-, C7.2, C9.2, C11.2, C13.2, C15.-, C17.1, C18.1, C19.-, C23.1, C25.1, C29.-, C39.2, C40.2, IC1.11 (V-), IC2.14 (GND1), IC2.24 (GND2), IC2.34 (GND3), IC2.44 (GND4), IC2.52 (GND5), IC2.60 (AGND), IC6.11 (V-), JP1.1, JP2.1, JP3.1, JP4.1, JP5.1, JP7.1, JP8.1, JP9.1, JP14.1, JP15.1, JP16.1, JP17.1, JP18.1, LED1.C, LED2.C, LED3.C, LED4.C, LED5.C, LED6.C, LED7.C, LED8.C, LED9.C, R2.1 (A), R11.1, R14.1, R15.1 (A), S1.2, S2.2, S3.2, S4.2, T4.2 (E), U1.1 (ADJ), U4.3 (VCC), U$1.3 (PGND1), U$1.4 (PGND1.), U$1.9 (PGND2), U$1.10 (PGND2.), U$1.18 (GND), U$2.3 (PGND1), U$2.4 (PGND1.), U$2.9 (PGND2), U$2.10 (PGND2.), U$2.18 (GND), U$3.3 (PGND1), U$3.4 (PGND1.), U$3.9 (PGND2), U$3.10 (PGND2.), U$3.18 (GND), U$4.3 (PGND1), U$4.4 (PGND1.), U$4.9 (PGND2), U$4.10 (PGND2.), U$4.18 (GND)
IR_OUT: IC2.5 (PA7), U4.1 (OUT)
LED_0: IC2.17 (PC1), R9.2
LED_1: IC2.47 (PF1), R7.2
LED_2: IC2.48 (PF2), R3.2
LED_3: IC2.49 (PF3), R8.2
LED_4: IC2.50 (PF4), R4.2
LED_5: IC2.51 (PF5), R1.2
LED_6: IC2.54 (PF6), R5.2
LED_7: IC2.55 (PF7), R21.2
M1_IN1: IC2.10 (PB4), U$1.17 (BIN1), U$1.21 (AIN1), U$2.17 (BIN1), U$2.21 (AIN1)
M1_IN2: IC2.11 (PB5), U$1.16 (BIN2), U$1.22 (AIN2), U$2.16 (BIN2), U$2.22 (AIN2)
M1_OUT_1: JP6.4, U$1.1 (A01), U$1.2 (A01.), U$1.11 (B01), U$1.12 (B01.), U$2.1 (A01), U$2.2 (A01.), U$2.11 (B01), U$2.12 (B01.)
M1_OUT_2: JP6.3, U$1.5 (A02), U$1.6 (A02.), U$1.7 (B02), U$1.8 (B02.), U$2.5 (A02), U$2.6 (A02.), U$2.7 (B02), U$2.8 (B02.)
M1_PWM: IC2.16 (PC0), U$1.15 (PWMB), U$1.23 (PWMA), U$2.15 (PWMB), U$2.23 (PWMA)
M2_IN1: IC2.12 (PB6), U$3.17 (BIN1), U$3.21 (AIN1), U$4.17 (BIN1), U$4.21 (AIN1)
M2_IN2: IC2.13 (PB7), U$3.16 (BIN2), U$3.22 (AIN2), U$4.16 (BIN2), U$4.22 (AIN2)
M2_OUT_1: JP6.2, U$3.1 (A01), U$3.2 (A01.), U$3.11 (B01), U$3.12 (B01.), U$4.1 (A01), U$4.2 (A01.), U$4.11 (B01), U$4.12 (B01.)
M2_OUT_2: JP6.1, U$3.5 (A02), U$3.6 (A02.), U$3.7 (B02), U$3.8 (B02.), U$4.5 (A02), U$4.6 (A02.), U$4.7 (B02), U$4.8 (B02.)
M2_PWM: IC2.26 (PD0), U$3.15 (PWMB), U$3.23 (PWMA), U$4.15 (PWMB), U$4.23 (PWMA)
unnamed: LED1.A, R1.1
unnamed: LED5.A, R4.1
unnamed: LED6.A, R5.1
unnamed: LED3.A, R3.1
unnamed: LED7.A, R7.1
unnamed: LED8.A, R8.1
unnamed: LED9.A, R9.1
unnamed: R13.2, U4.2 (GND)
unnamed: JP10.2, JP10.3
unnamed: D1.C, R12.2, U$13.P$2
unnamed: IC2.56 (PDI_DATA), JP18.6
unnamed: IC2.57 (RESET), JP18.2, R6.1
unnamed: JP10.1, JP14.2
unnamed: IC1.6 (-IN), IC1.9 (-IN), IC1.13 (-IN), R2.2 (S)
unnamed: D1.A, T4.3 (C), U$13.P$1
unnamed: R20.1, T4.1 (B)
unnamed: IC6.2 (-IN), IC6.6 (-IN), IC6.9 (-IN), IC6.13 (-IN), R15.2 (S)
unnamed: JP15.2, R14.2
unnamed: IC1.3 (+IN), R10.1, R11.2
unnamed: C40.1, IC2.58 (PR0), Q2.1
unnamed: C39.1, IC2.59 (PR1), Q2.2
unnamed: LED2.A, R19.1
unnamed: LED4.A, R21.1
SHARP1_OUT: IC1.5 (+IN), IC2.63 (PA1), JP5.3
SHARP2_OUT: IC1.10 (+IN), IC2.64 (PA2), JP7.3
SHARP3_OUT: IC1.12 (+IN), IC2.1 (PA3), JP8.3
SHARP_INT_1: IC1.7 (OUT), IC2.23 (PC7)
SHARP_INT_2: IC1.8 (OUT), IC2.22 (PC6)
SHARP_INT_3: IC1.14 (OUT), IC2.4 (PA6)
SONAR2_ECHO: IC2.28 (PD2), JP17.2
SONAR2_TRIG: IC2.29 (PD3), JP17.3
SONAR_ECHO: IC2.30 (PD4), JP16.2
SONAR_TRIG: IC2.31 (PD5), JP16.3

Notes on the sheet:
LEDS
BUZZER
EDGE SENS
ANALOG SHARPS
DIGITAL SHARPS
& OTHER
PSU
BUTTONS
UNUSED PINS
DISPLAY
ANALOG SECTION
SONAR
D_SHARP

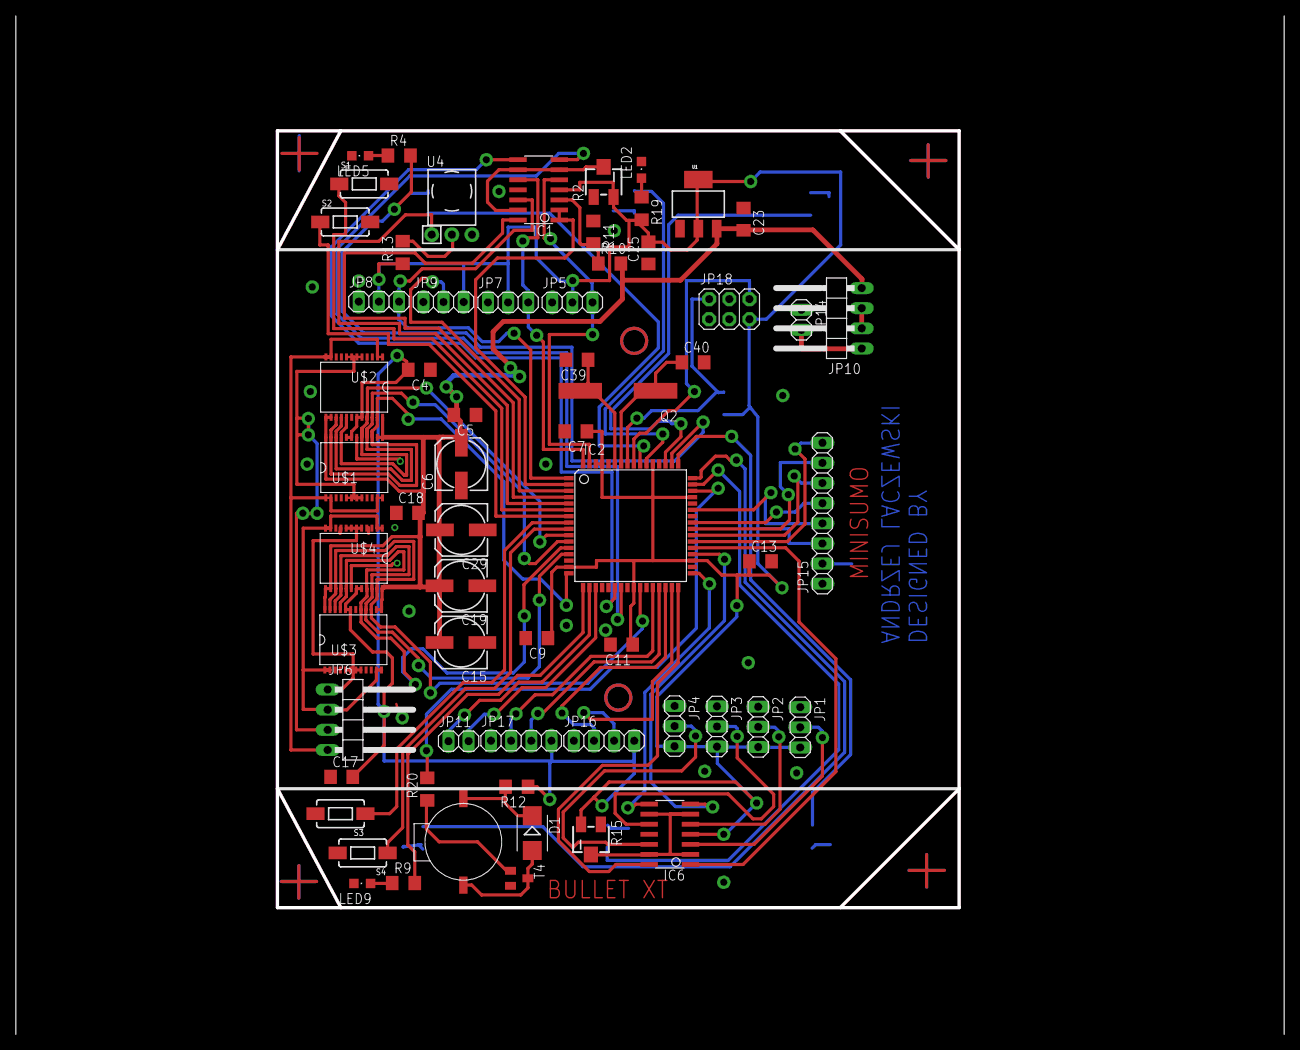
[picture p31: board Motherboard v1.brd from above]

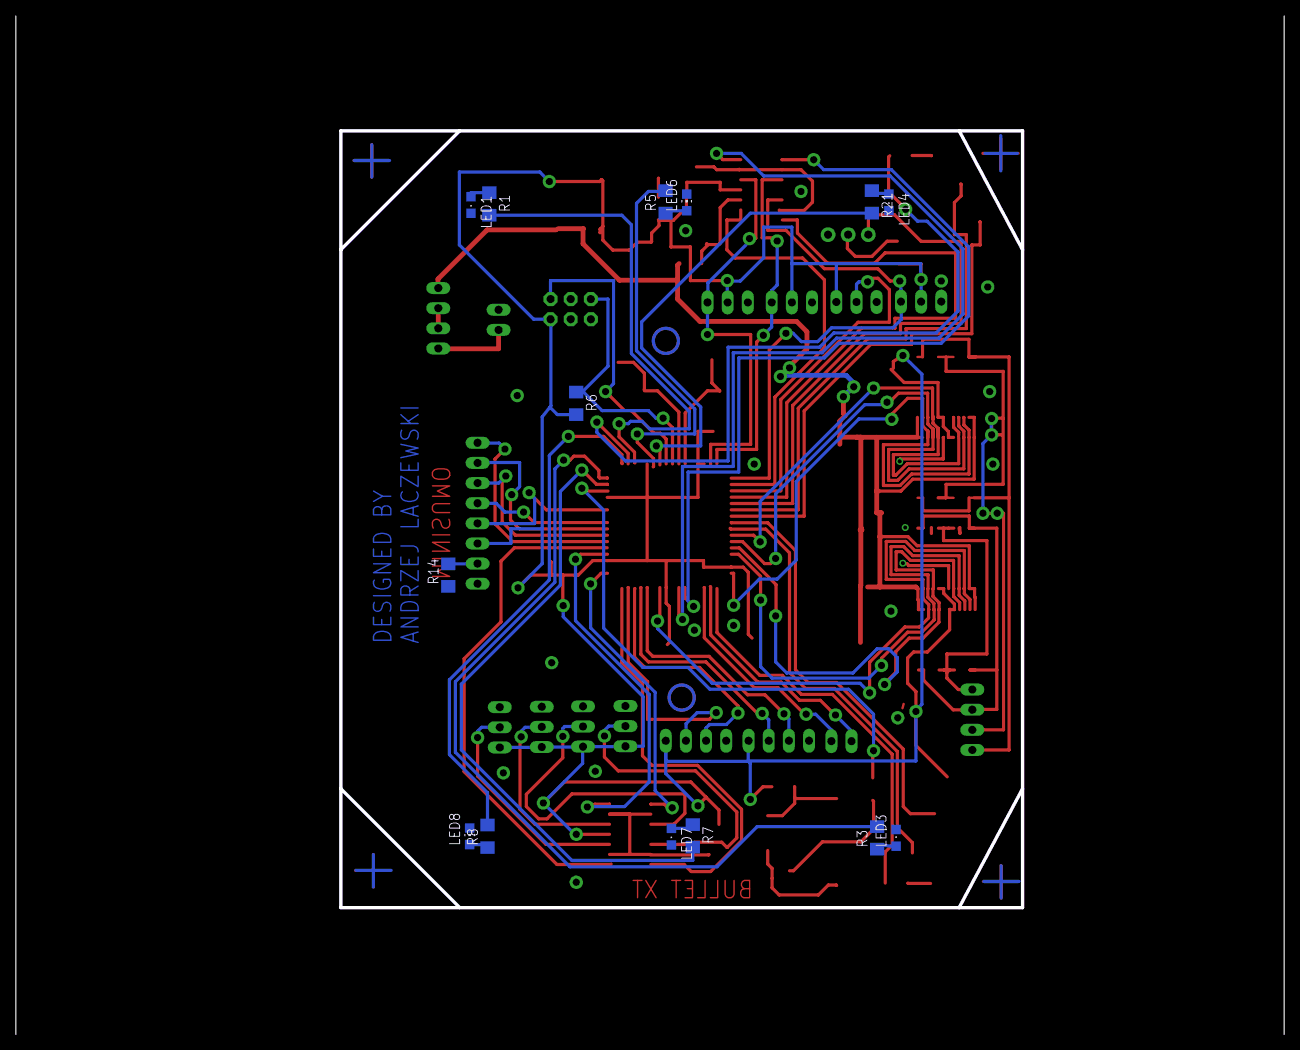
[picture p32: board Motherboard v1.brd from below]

Board: 2 copper layers, 86.0 x 98.0 mm, 76 parts (14 on the bottom side), 77 nets.

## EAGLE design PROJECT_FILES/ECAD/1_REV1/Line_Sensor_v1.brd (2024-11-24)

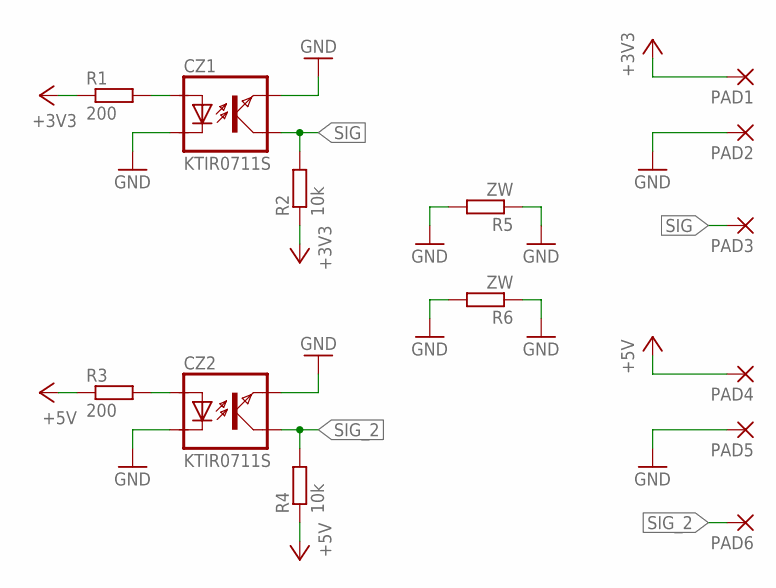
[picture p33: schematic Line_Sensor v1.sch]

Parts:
CZ1, CZ2: KTIR0711S; TOP
PAD1, PAD2, PAD3, PAD4, PAD5, PAD6: SMD5; SMD2,54-5,08
R1, R3: 200; R1206
R2, R4: 10k; R1206
R5, R6: ZW; R1206

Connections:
+3V3: PAD1.1, R1.1, R2.1
+5V: PAD4.1, R3.1, R4.1
GND: CZ1.EMITER, CZ1.KATODA, CZ2.EMITER, CZ2.KATODA, PAD2.1, PAD5.1, R5.1, R5.2, R6.1, R6.2
unnamed: CZ1.ANODA, R1.2
unnamed: CZ2.ANODA, R3.2
SIG: CZ1.KOLEKTOR, PAD3.1, R2.2
SIG_2: CZ2.KOLEKTOR, PAD6.1, R4.2

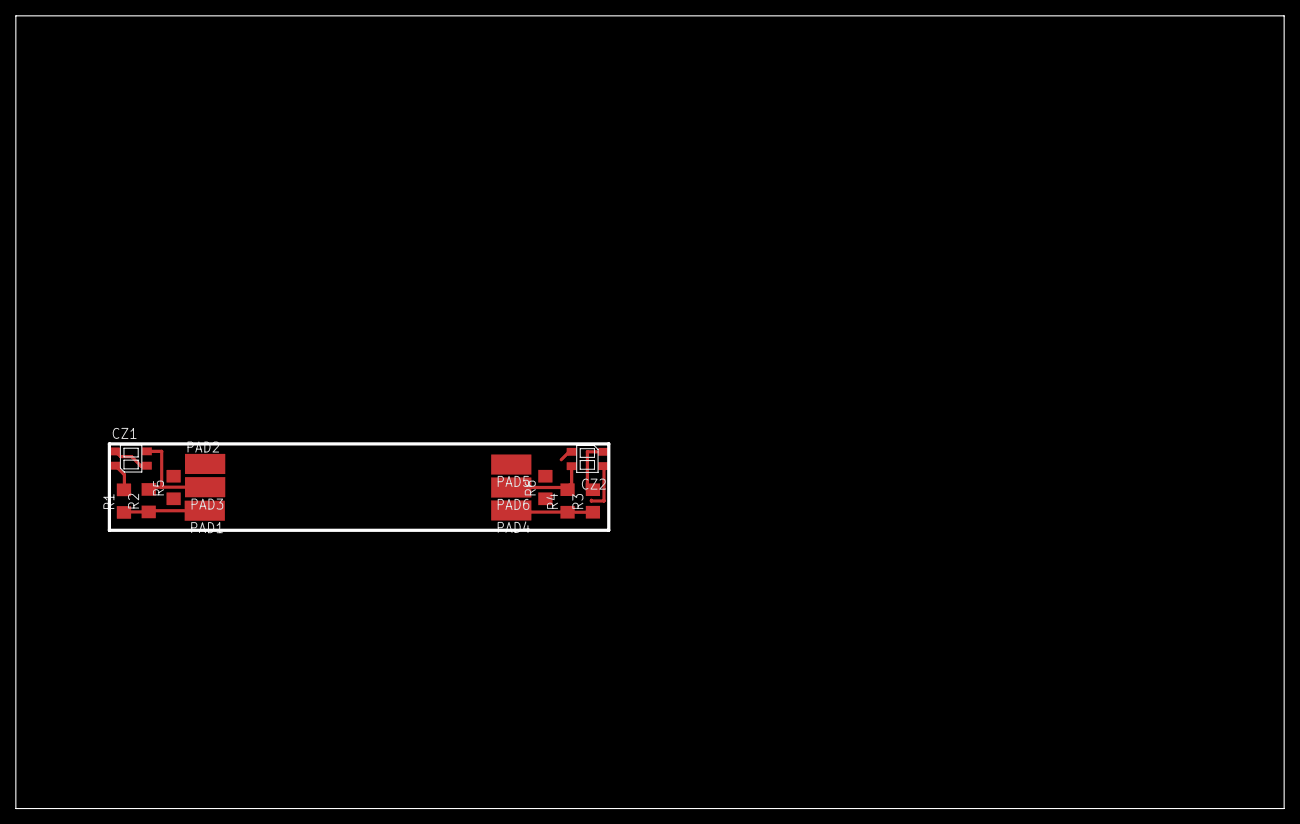
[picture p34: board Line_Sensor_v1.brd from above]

Board: 2 copper layers, 160.0 x 100.0 mm, 14 parts (0 on the bottom side), 7 nets.

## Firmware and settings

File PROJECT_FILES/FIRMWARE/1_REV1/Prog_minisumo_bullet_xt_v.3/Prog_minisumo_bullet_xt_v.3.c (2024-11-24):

#include "Includes.h"

int main(void)
{
	init_OSC_PLL(PLL_FACT);
	init_PORTS();
	init_USART_C0();
	init_ADC();
	init_SPI_LCD();
	init_MOT_PWM();
	init_TIM_0E();
	init_TIM_0F();
	init_RTC();
	init_PMIC();
	BUZZ_beep(200);
	init_LCD();
	GP_FLAGS_s.MODE =MODE_STANDARD;
	SENS_FLAG_s.SHARP_DIGIT=0;
	GP_FLAGS_s.FIRST_TURN=1;
	
	uint32_t start=0;

	while(1)
	{
		LCD_menu_handle();
		if (GP_FLAGS_s.START_STOP == 1)
		{
			switch (GP_FLAGS_s.MODE)
			{
				case MODE_TORNADO :
				
				// 				if(GP_FLAGS_s.FIRST_TURN==1)
				// 				{
				// 					//Wait_5_sec();
				// 					GP_FLAGS_s.FIRST_TURN=0;
				// 				}
				//
				//  				while(GP_FLAGS_s.START_STOP == 1)
				//  				{
				//
				// //					MOT_turn_right(30);
				// // 					if (SENS_FLAG_s.SHARP_A_FRONT==1)
				// // 					{
				// // 						MOT_brake();
				// // 						_delay_ms(50);
				// // 						MOT_go_forward(70);
				// // 						_delay_ms(250);
				// // 						SENS_FLAG_s.SHARP_A_FRONT=0;
				// // 					}
				//
				// // 					else
				// // 					{
				// // 						MOT_turn_right(30);
				// // 					}
				// //
				// // 					if (DIGITAL_SHARP_CHECK)
				// // 					{
				// // 						MOT_go_forward(60);
				// // 						_delay_ms(50);
				// // 					}
				// // 					else
				// // 					{
				// // 						MOT_turn_right(30);
				// // 					}
				//
				//
				// 					//----------------------------------------------------------------LINE::::---->>>>>
				//
				//
				//
				// 					if ((SENS_FLAG_s.LINE_LEFT==1 && SENS_FLAG_s.LINE_RIGHT==1)&&read_rtc_time()-IGNEORE_SENS_s.LINE>250) // line sense escape + delay
				// 					{
				// 						MOT_brake();
				// 						_delay_ms(20);
				// 						//MOT_go_backward(90);
				//
				// 						for (uint16_t i=0;i<100;i++)
				// 						{
				// 							MOT_go_backward(i);
				// 							_delay_ms(1);
				// 						}
				// 						MOT_go_backward(90);
				// 						_delay_ms(60);
				// 						MOT_brake();
				//
				// 						MOT_turn_180_deg(DIR_RIGHT);
				//
				// 						SENS_FLAG_s.LINE_RIGHT=0;
				// 						SENS_FLAG_s.LINE_LEFT=0;
				// 						IGNEORE_SENS_s.LINE = read_rtc_time();
				// 						BUZZ_beep(10);
				// 					}
				//
				// 					if ( SENS_FLAG_s.LINE_RIGHT==1 && read_rtc_time()-IGNEORE_SENS_s.LINE>250) // line sense escape + delay
				// 					{
				// 						MOT_brake();
				// 						_delay_ms(20);
				// 						//MOT_go_backward(90);
				//
				// 						for (uint16_t i=0;i<100;i++)
				// 						{
				// 							MOT_go_backward(i);
				// 							_delay_ms(1);
				// 						}
				//
				// 						MOT_go_backward(90);
				// 						_delay_ms(60);
				// 						MOT_brake();
				//
				// 						MOT_turn_90_deg(DIR_LEFT);
				//
				// 						MOT_turn_left(50);
				// 						_delay_ms(60); // turn a little more
				// 						MOT_brake();
				//
				// 						SENS_FLAG_s.LINE_RIGHT=0;
				// 						SENS_FLAG_s.LINE_LEFT=0;
				// 						IGNEORE_SENS_s.LINE = read_rtc_time();
				// 						BUZZ_beep(10);
				// 					}
				//
				// 					if (SENS_FLAG_s.LINE_LEFT==1 && read_rtc_time()-IGNEORE_SENS_s.LINE>250) // line sense escape + delay
				// 					{
				// 						MOT_brake();
				// 						_delay_ms(20);
				//
				// 						for (uint16_t i=0;i<100;i++)
				// 						{
				// 							MOT_go_backward(i);
				// 							_delay_ms(1);
				// 						}
				//
				// 						MOT_go_backward(90);
				// 						_delay_ms(60);
				// 						MOT_brake();
				//
				// 						MOT_turn_90_deg(DIR_RIGHT);
				//
				// 						MOT_turn_right(50);
				// 						_delay_ms(60);
				// 						MOT_brake();
				//
				// 						SENS_FLAG_s.LINE_RIGHT=0;
				// 						SENS_FLAG_s.LINE_LEFT=0;
				// 						IGNEORE_SENS_s.LINE = read_rtc_time();
				// 						BUZZ_beep(50);
				// 					}
				//
				// 					if (SENS_FLAG_s.SHARP_A_FRONT==1)
				// 					{
				// 						MOT_brake();
				// 						MOT_go_forward(40);
				//
				// 						IGNEORE_SENS_s.SHARP_A_FRONT  = read_rtc_time();
				// 						while(read_rtc_time()-IGNEORE_SENS_s.SHARP_A_FRONT <1000 && DIGITAL_SHARP_CHECK)
				// 						{
				// 							//	if (SENS_FLAG_s.SHARP_A_LEFT==1)break; // we have sensed left sharp so we dont clear flag and go out that loop
				// 							//	if (SENS_FLAG_s.SHARP_A_RIGHT==1)break;
				// 								if (SENS_FLAG_s.LINE_LEFT==1)break;// we have sensed that during comeup we are on the line so break and dont clear flag
				// 								if (SENS_FLAG_s.LINE_RIGHT==1)break;
				// 						}
				// 						MOT_brake();
				// 						SENS_FLAG_s.SHARP_A_FRONT=0;
				// 					}
				// 					else
				// 					{
				// 							MOT_turn_right(35);
				// 					}
				//
				// 					// to dac to wew petli od frontu bo nie mozemy skerecec podczas wolnej jazdy
				//
				// 					if (SENS_FLAG_s.SHARP_A_LEFT==1 && read_rtc_time()-IGNEORE_SENS_s.SHARP_A_LEFT>100) //&& SENS_FLAG_s.LINE_LEFT==0 && SENS_FLAG_s.LINE_RIGHT==0) // czy to nie musi byc przed frontowym?
				// 					{
				// 						MOT_turn_45_deg(DIR_LEFT);
				// 						SENS_FLAG_s.SHARP_A_LEFT=0;
				// 						IGNEORE_SENS_s.SHARP_A_LEFT = read_rtc_time();
				// 					}
				//
				// 					if (SENS_FLAG_s.SHARP_A_RIGHT==1 && read_rtc_time()-IGNEORE_SENS_s.SHARP_A_RIGHT>100)// && SENS_FLAG_s.LINE_LEFT==0 && SENS_FLAG_s.LINE_RIGHT==0)
				// 					{
				// 						MOT_turn_45_deg(DIR_RIGHT);
				// 						SENS_FLAG_s.SHARP_A_RIGHT=0;
				// 						IGNEORE_SENS_s.SHARP_A_RIGHT = read_rtc_time();
				// 					}
				//
				//
				// 				}
				//
				//
				
				break;
				
				case MODE_LF :
				break;
				
				case MODE_STANDARD :
				
				//----------first rotate
				if(GP_FLAGS_s.FIRST_TURN==1)
				{
					Wait_5_sec();
					MOT_turn_right(30);
					_delay_ms(50); // opoznienie dla klapki
					IGNEORE_SENS_s.SHARP_A_FRONT  = read_rtc_time();
					while(read_rtc_time()-IGNEORE_SENS_s.SHARP_A_FRONT <650 && (SENS_FLAG_s.LINE_LEFT==0 && SENS_FLAG_s.LINE_RIGHT==0))
					{
						if (SENS_FLAG_s.SHARP_A_FRONT==1||SENS_FLAG_s.SHARP_DIGIT==1)
						{
							MOT_go_forward(40);
							SENS_FLAG_s.SHARP_A_LEFT=0;
							SENS_FLAG_s.SHARP_A_RIGHT=0;
							break;
						}
					}
					if (SENS_FLAG_s.SHARP_A_FRONT==0 && SENS_FLAG_s.SHARP_DIGIT==0)
					{
						MOT_brake();
					}
					GP_FLAGS_s.FIRST_TURN=0;
				}
				else
				{
					MOT_go_forward(40);
				}
				
				//----------------------------------------------------------------LINE::::---->>>>>
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

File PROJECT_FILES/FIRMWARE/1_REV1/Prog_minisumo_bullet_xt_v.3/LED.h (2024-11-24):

/*
 * LED.h
 *
 * Created: 2016-05-31 17:18:49
 *  Author: Andrzej
 */ 


#ifndef LED_H_
#define LED_H_
#include "Includes.h"

#define LED_1_ON	    PORTF.OUTSET = PIN1_bm;
#define LED_2_ON		PORTF.OUTSET = PIN2_bm;
#define LED_3_ON		PORTF.OUTSET = PIN3_bm;
#define LED_4_ON		PORTF.OUTSET = PIN4_bm;
#define LED_5_ON		PORTF.OUTSET = PIN5_bm;
#define LED_6_ON		PORTF.OUTSET = PIN6_bm;
#define LED_7_ON		PORTF.OUTSET = PIN7_bm;
#define LED_8_ON		PORTC.OUTSET = PIN1_bm;

#define LED_1_OFF		PORTF.OUTCLR = PIN1_bm;
#define LED_2_OFF		PORTF.OUTCLR = PIN2_bm;
#define LED_3_OFF		PORTF.OUTCLR = PIN3_bm;
#define LED_4_OFF		PORTF.OUTCLR = PIN4_bm;
#define LED_5_OFF		PORTF.OUTCLR = PIN5_bm;
#define LED_6_OFF		PORTF.OUTCLR = PIN6_bm;
#define LED_7_OFF		PORTF.OUTCLR = PIN7_bm;
#define LED_8_OFF		PORTC.OUTCLR = PIN1_bm;

#define LED_1_TOG       PORTF.OUTTGL = PIN1_bm;
#define LED_2_TOG       PORTF.OUTTGL = PIN2_bm;
#define LED_3_TOG       PORTF.OUTTGL = PIN3_bm;
#define LED_4_TOG       PORTF.OUTTGL = PIN4_bm;
#define LED_5_TOG       PORTF.OUTTGL = PIN5_bm;
#define LED_6_TOG       PORTF.OUTTGL = PIN6_bm;
#define LED_7_TOG       PORTF.OUTTGL = PIN7_bm;
#define LED_8_TOG       PORTC.OUTTGL = PIN1_bm;

void LED_blink(void);
void LED_toggle(void);


#endif /* LED_H_ */

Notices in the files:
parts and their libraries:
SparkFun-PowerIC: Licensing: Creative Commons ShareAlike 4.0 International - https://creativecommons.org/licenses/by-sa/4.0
